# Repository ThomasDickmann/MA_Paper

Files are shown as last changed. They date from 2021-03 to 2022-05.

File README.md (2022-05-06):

# An adaptive mechatronic exoskeleton for force-controlled finger rehabilitation
>This repository represents the source code for a novel mechatronic exoskeleton architecture for finger rehabilitation. The system consists of an underactuated kinematic structure that enables the exoskeleton to act as an adaptive finger stimulator. 

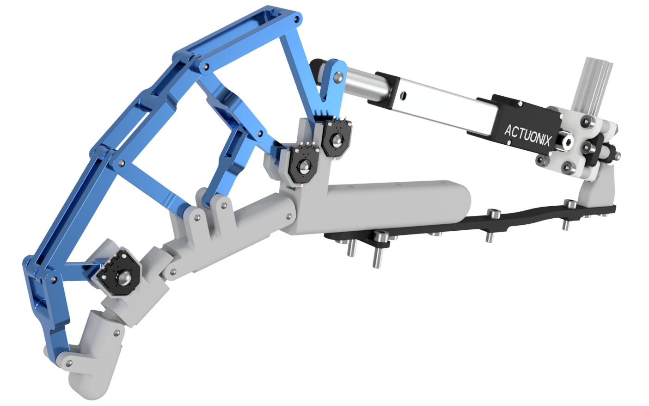
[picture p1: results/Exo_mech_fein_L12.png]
 

## Setup

* Install Matlab

## What does each file do? 

    .     
    ├── MATLAB_Functions                 # Folder for all functions in 'm' format
    |   |
    │   ├── CSV_Interpretation.m         # calculates diagnostic data from .csv
    │   ├── getActuationAngle.m          # determines the angle phi_1 at point B depending the actor
    │   ├── getActuationForce.m          # calculates the external force of the actuator
    │   ├── getActuationSignal.m         # determines the delta_s position of the actuator from phi_1
    │   ├── getAngle.m                   # finds the angle of a vector (r_i) in the worldframe
    │   ├── getConstParam.m              # calculation of the const parameters depending on the finger
    │   ├── getExtForces.m               # determines the external forces of the exoskeleton
    │   ├── getJointAngles.m             # calculates the finger joint angles from the joint positions
    │   ├── getJointAnglesDeg.m          # in Degrees
    │   ├── getJointAnglesRad.m          # in Rad
    │   ├── getJointTorques.m            # calculates the finger moments for the quasistatic state
    │   ├── getKinConfig.m               # position of all joints of the kinematics from the encoders
    │   ├── getPhalanxForces.m           # rotates the external forces on the phalanges
    │   ├── getPoint.m                   # position of a joint in the world system
    │   ├── plotBR.m                     # plots the range of motion of the index finger
    │   ├── plotBR_alternative.m         # alternative to plotBR.m
    │   └── plotKinConfig.m              # plots the current kinematic position 
    |
    ├── MATLAB_Models                    # Folder for all models in 'm' format 
    |   |
    |   ├── Calibration_curves_potentiometer.m        # contains the calibration data of the position sensors
    |   ├── Force_Equilibrium_SoE.m                   # creates a linear system of equations from the equilibrium conditions around each joint
    |   ├── Force_Sensor_Drift_Hysteresis_Test.m      # interpretation of force sensor data
    |   ├── Integrated_Force_Sensor_test.m            # simplified force sensor calibration for recalibrating the integrated sensors
    |   ├── Interpretation_Script_CSV_Files.m         # script which utilizes the CSV_Interpretation.m function to create arrays with interpreted data
    |   ├── Linear_Interpolation_Potentiometer.m      # linear interpolation concept used for position sensor calibration  
    |   ├── Newton_Euler_generation_script.m          # creates the full NE model of the finger using the symbolic toolbox
    |   ├── Plot_ROM_Index_Finger.m                   # plots the range of motion of the index finger based on joint angle data arrays
    |   ├── Plot_interpreted_CSV_values.m             # plots the interpreted .csv test data
    |   ├── Single_sensor_dataset_interpretation.m    # exemplary interpretation of a singe test data set (3 joint angles, 2 forces)
    |   
    └── results.txt                      # Folder for all result images, test data and CAD files for printing (.stl)

# Citation

If you use this project in any of your work, please cite:

```
Dickmann  T, Wilhelm NJ, Glowalla  C, Haddadin  S, van der Smagt  P and Burgkart  R (2021) An Adaptive Mechatronic Exoskeleton for Force-Controlled Finger Rehabilitation. Front. Robot. AI 8:716451. doi: 10.3389/frobt.2021.716451
```

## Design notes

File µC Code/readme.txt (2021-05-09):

Code for Teensy 4.1 with modified Teensyduino Beta Version -> Enables usage of standard <sd.h> library/commands with <sdfat.h> functionality

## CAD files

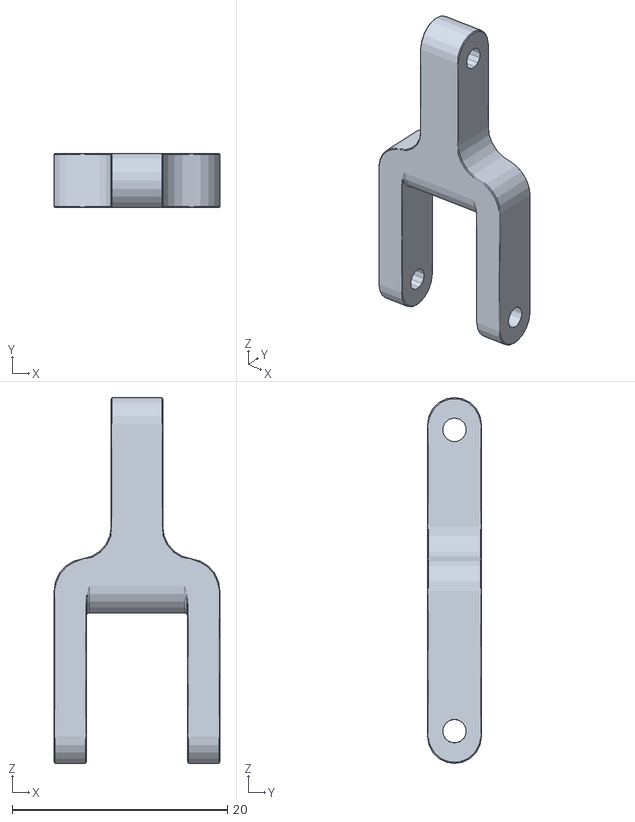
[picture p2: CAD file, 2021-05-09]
results/CAD/l_12.stl
15.4 x 5.00 x 34.0

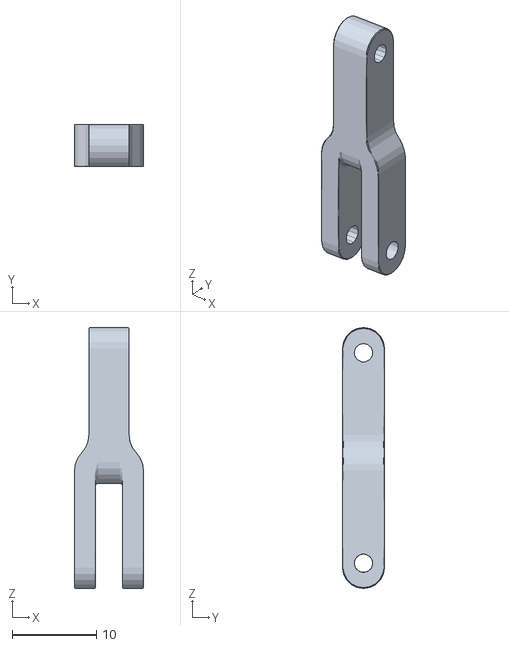
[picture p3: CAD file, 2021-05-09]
results/CAD/l_6.stl
8.20 x 5.00 x 31.0

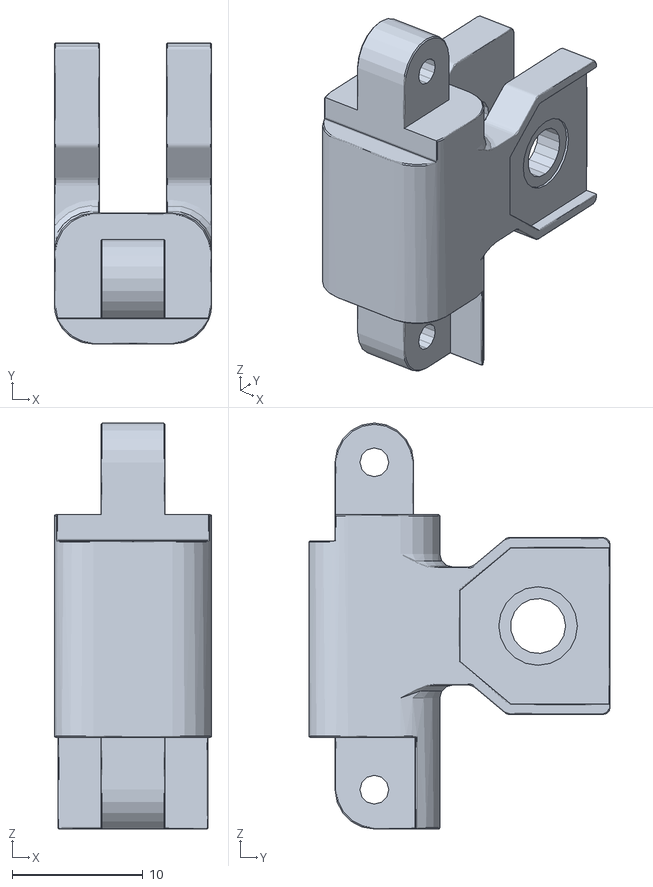
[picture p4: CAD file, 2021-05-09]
results/CAD/Phalanx_Media.stl
12.0 x 23.0 x 31.0

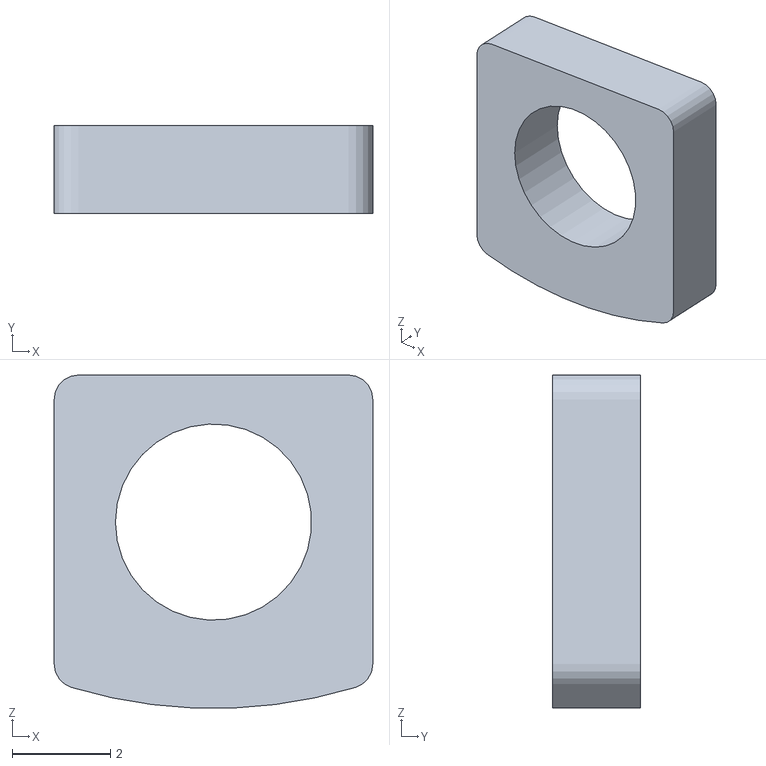
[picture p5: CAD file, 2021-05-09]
results/CAD/Aktor_Inlay.stl
6.50 x 1.80 x 6.79

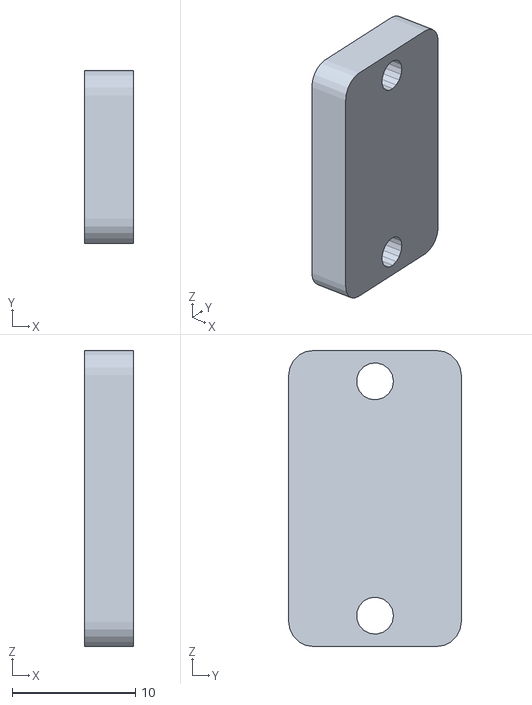
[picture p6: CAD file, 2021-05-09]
results/CAD/Sensoraufnahme.stl
4.00 x 14.0 x 24.0

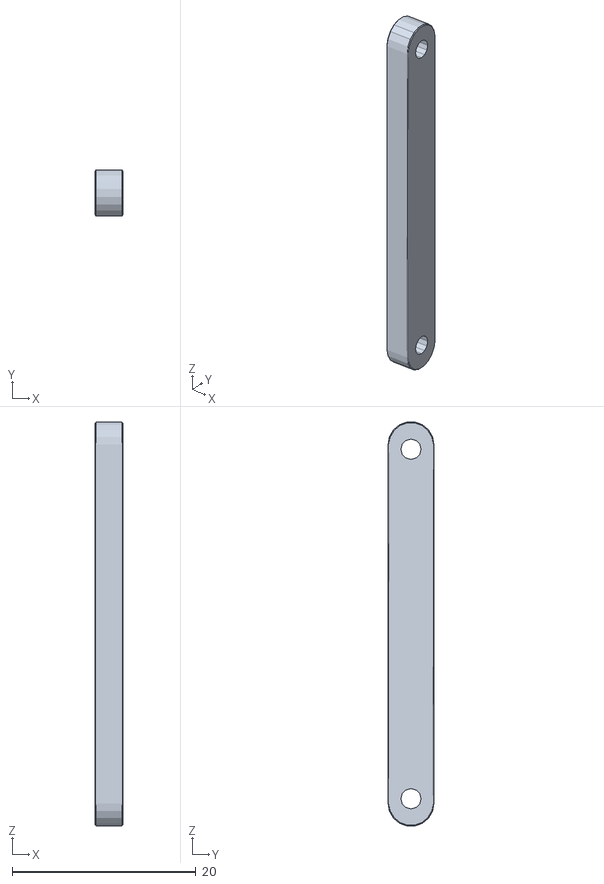
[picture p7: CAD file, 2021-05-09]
results/CAD/l_10__2x_drucken.stl
3.00 x 5.00 x 43.9

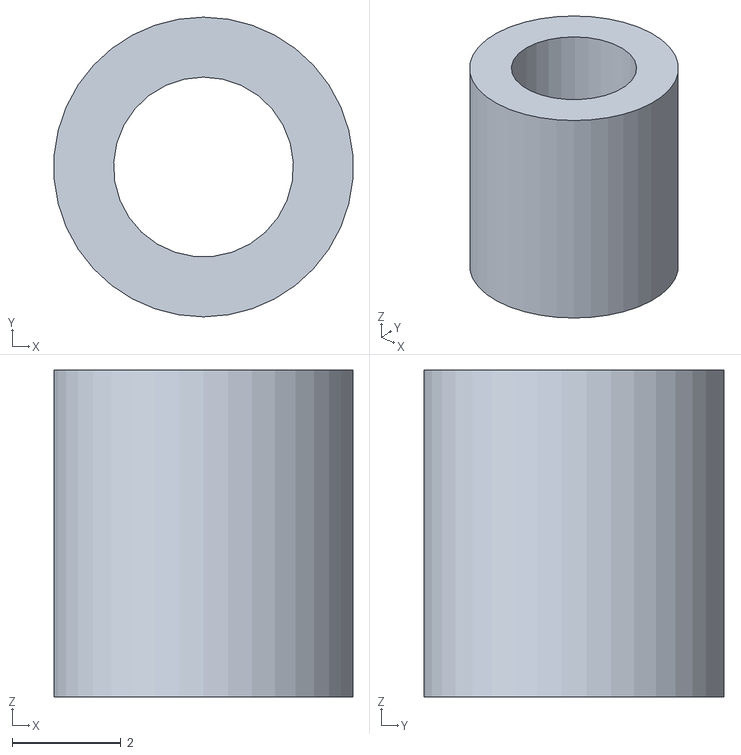
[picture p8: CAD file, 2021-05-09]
results/CAD/Standoffs_6x.stl
5.48 x 5.50 x 6.00

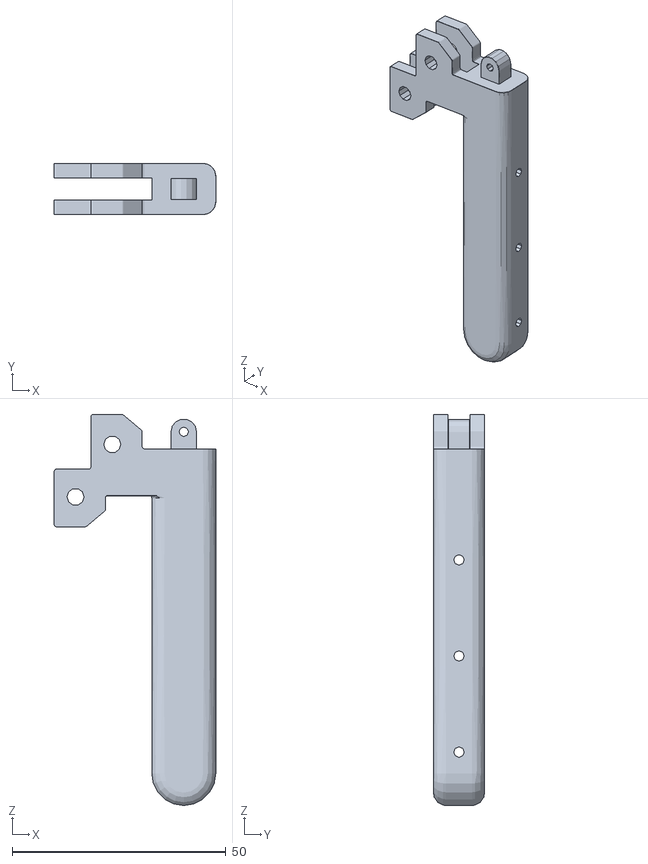
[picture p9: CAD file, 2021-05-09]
results/CAD/Metacarpal.stl
37.8 x 12.0 x 91.5

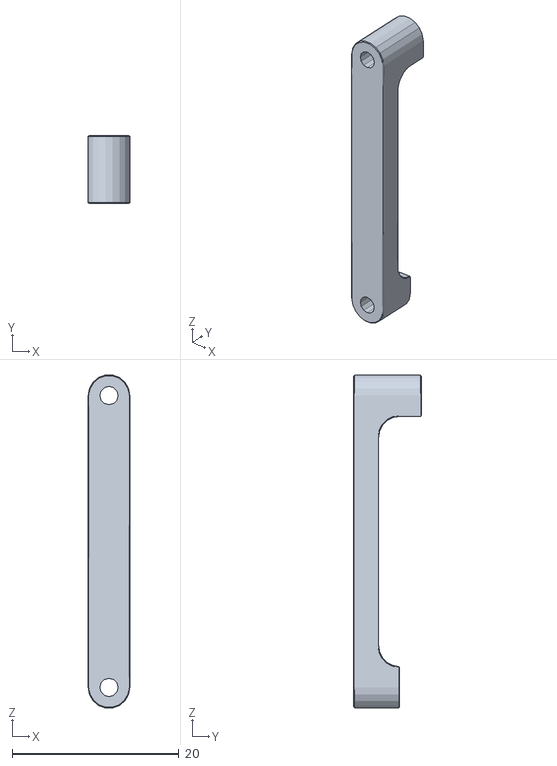
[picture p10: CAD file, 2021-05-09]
results/CAD/l_2__2x_drucken.stl
5.00 x 8.10 x 39.9

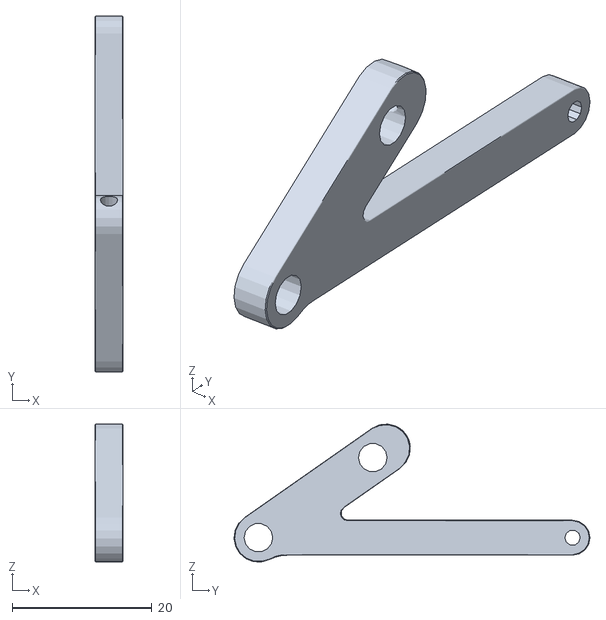
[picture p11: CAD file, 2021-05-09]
results/CAD/l_1.stl
4.00 x 51.0 x 19.7

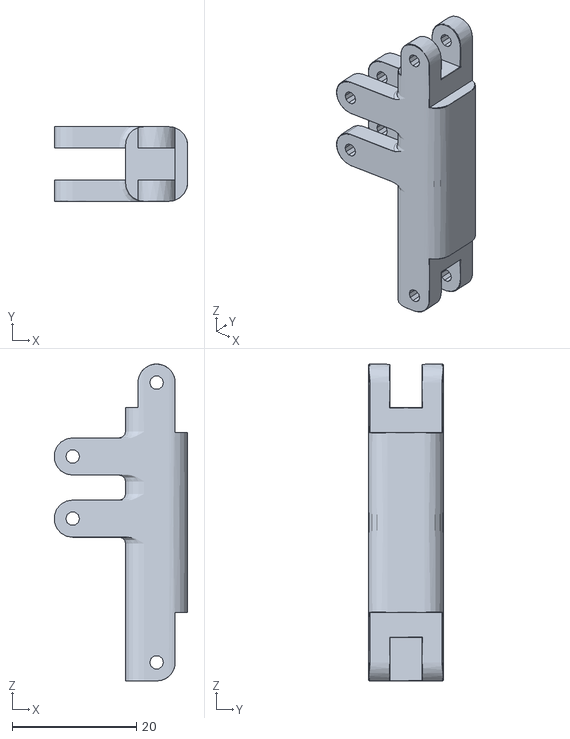
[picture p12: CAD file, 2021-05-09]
results/CAD/Phalanx_Proximalis.stl
21.5 x 12.0 x 51.0

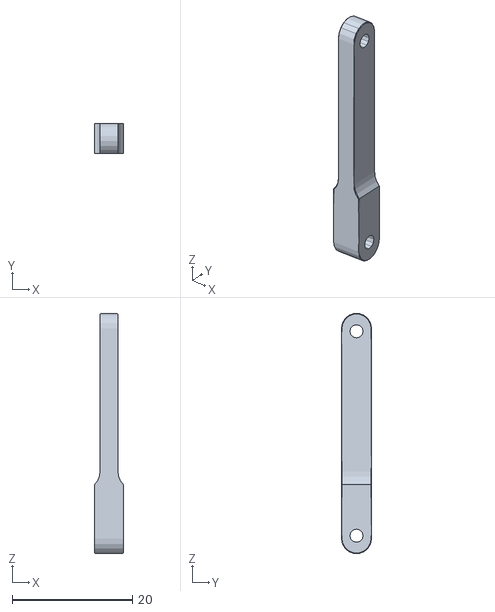
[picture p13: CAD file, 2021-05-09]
results/CAD/l_8.stl
4.80 x 5.00 x 39.9

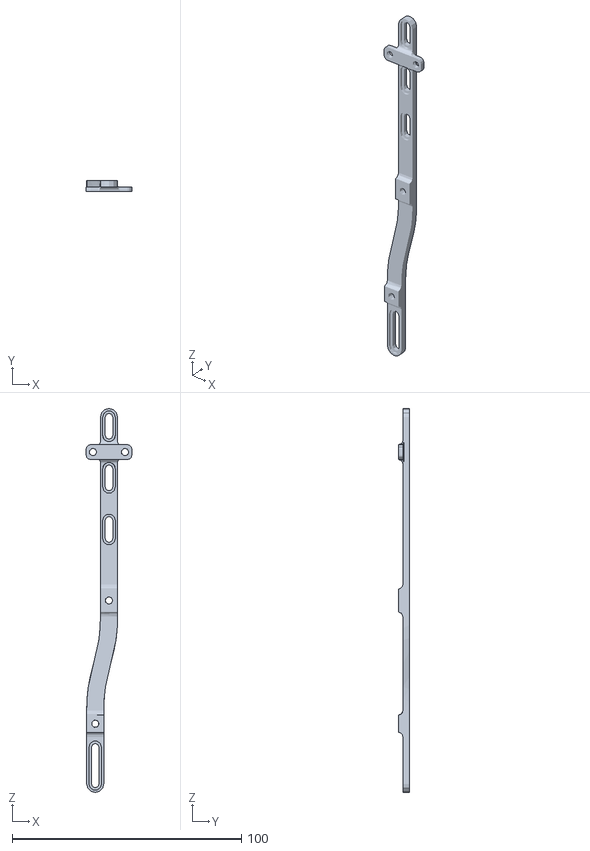
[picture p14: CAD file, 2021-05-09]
results/CAD/Aktoraufnahme.stl
20.0 x 5.00 x 167.5

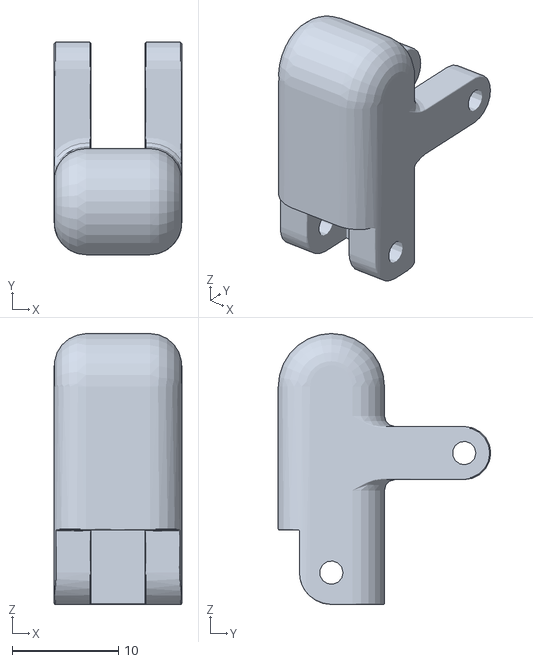
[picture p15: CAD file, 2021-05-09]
results/CAD/Phalanx_Distalis.stl
12.0 x 20.0 x 25.5

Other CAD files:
results/CAD/l_3.stl
results/CAD/l_7.stl
results/CAD/Att_Base.stl
results/CAD/Klemmelement_2x.stl
results/CAD/Gelenkmount.stl
results/CAD/Mount.stl
results/CAD/l_11.stl
results/CAD/l_4.stl

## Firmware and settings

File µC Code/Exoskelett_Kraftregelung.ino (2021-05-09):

#include <SD.h>
#include <math.h> 

//Vorbereitung SD Karte /////////////////////////////////////////////
File dataFile; //Fileobjekt für SD Karte erzeugen

//Aufruf in Setup, Karteninitialisierung
void initCard()
{
  bool ret;
  Serial.print("Initialisiere SD Karte...");
  ret = SD.begin(BUILTIN_SDCARD);
  if (!ret) {
    Serial.println("Card failed, or not present");
    while (1) {
    }
  }
  Serial.println("Karte initialisiert.");
  }

//Aufruf in Setup, Vorbereitung des dataFile zum beschreiben
bool openFile_write(const char *filename)
{
  dataFile = SD.open(filename, FILE_WRITE);  
  dataFile.flush();
  return (dataFile==true);
}
///////////////////////////////////////////////////////////////////////

//Laufzeit und Loggingfrequenz einstellen ////////////////////////////
//Setzen von fester Loopedauer über Timer im Hintergrund, sodass der Controller parallel arbeiten kann
unsigned int loopTime = 10; //Wert für gewünschtes Loopintervall in Millisekunden
unsigned long breakTime; //Zeitstempel zu Anfang des Loops -> Ablegen des Zeitpunkts für Loopende

//Counter für gewünschte Anzahl an Loopdurchläufen 
int totalRuns = 25000/loopTime; //(25 Sekunden pro Bewegung)
int t = 0; //Zählervariable für Loopdurchläufe
int k = 0; //Zählervariable für Funktion Aktortrajektorie
///////////////////////////////////////////////////////////////////////

//Verzögerung für Kraftsensormessungen 

int t_del = 3000;

//Parametrierung der Aktorik///////////////////////////////////////////
const float l_akt = 139.3f; //102mm Aktorlänge von Loch zu Loch + Kraftsensorlänge von 37.3mm 
const float d_b = 161.062f; //Abstand Glelenk B zu Mountgelenk Aktorrückseite
const float akt_x = -160.761f; //Abstand in X-Richtung Welt KS Gelenk B zu Mountgelenk Aktorrückseite in mm 
const float akt_y = -9.845f; //Abstand Y-Richtung Gelenk B zu Mountgelenk Aktorrückseite in mm 
const float alpha_const = 0.0612f; //Winkel zwischen d_B und X-Achse Weltsysten in rad (3.5°)
const float theta = 0.6109f; //Winkel zwischen l_1 und l_2 in rad (35°)
const float l_s = 20.0f; //Kurzer Arm der Antriebsschwinge
//const float phi_B_min = 0.3491f; //20°, Minimalwert des Schwingenwinkels -> Berechnung max. Aktorstellung
const float phi_B_max = 2.2340f; //128°, Maximalwert des Schwingenwinkels -> Berechnung min. Aktorstellung 
//Überschreiben für Demo: Weniger Auslenkung
const float phi_B_min = 0.9235f; //30°
const float delta_phi_max = 108.000f; //Maximales Intervall der Antriebsschwinge in Grad
const float val_count_phi_B_max = 5.0f; //Startwert für Loopcounter, sodass Aktor aus seiner Minimalposition heraus startet (Anfahren in Setup-Funktion!)
const float pi = 3.1416f; //Konstante für Wert von pi erzeugen 
const float multip = (2*pi)/totalRuns; //Aufteilung von 2pi auf die gesamte Anzahl an Durchläufen
///////////////////////////////////////////////////////////////////////


//Funktionen zur Berechnung der Aktorvariablen/////////////////////////
//Berechnungen von Sollstellung s des Aktors aus Schwingenwinkelvorgabe [Verifiziert durch Vergleich mit MATLAB]
float getActuationSignal (float phi){
    float alpha = pi - theta - phi + alpha_const;
    //Serial.print("alpha= ");
    //Serial.println(alpha);
    float l = sqrtf((powf(l_s,2) + powf(d_b,2) - 2*l_s*d_b*cosf(alpha))); //Kosinussatz zur Berechnung der Gesamtlänge des Aktorverbands l
    //Serial.print("l= ");
    //Serial.println(l);
    float s_nom = l - l_akt;
    return s_nom; 
}

//Berechnung des aktuell anliegenden Antriebsmoments aus Schwingenwinkel und gemessener Aktorkraft [Verifiziert durch Vergleich mit MATLAB]
float getActuationTorque (float phi_B, float F_Aktor){
    float alpha_quer = pi - theta - phi_B;  //Winkel zwischen X-Achse und l_s
    //Serial.print("alpha_quer= ");
    //Serial.println(alpha_quer);
    float S_x = -l_s * cosf(alpha_quer); //x-Position der Spitze des kurzen Schwingenarms 
    float S_y = l_s * sinf(alpha_quer); //y-Position der Spitze des kurzen Schwingenarms 
    float phi_F = getAngle(akt_x,akt_y,S_x,S_y); // Funktion: Berechnet aktuellen Kraftvektorwinkel im Raum 
    //Serial.print("phi_F= ");
    //Serial.println(phi_F);
    float F_Akt_x = F_Aktor * cosf(phi_F); //Komponenten des Kraftvektors in Weltsystem
    float F_Akt_y = F_Aktor * sinf(phi_F);
    float M_akt = (F_Akt_x * S_y + F_Akt_y * (-S_x));  //[Nmm], Berechnen des Moments um Punkt B, pos. Richtung s. Skizze, pos. delta_x führt zu neg. Moment nach Skizze  
    return fabs(M_akt);
}

//Benötigte Funktion zur Berechnung des Kraftvektorwinkels [Verifiziert durch Vergleich mit MATLAB]
float getAngle(float p1_x, float p1_y, float p2_x, float p2_y){
    float delta_x = p2_x - p1_x; //akt_x und akt_y konst. Größen definiert in aktorik.h
    float delta_y = p2_y - p1_y;  
    float phi = 0;     
    if (delta_x > 0){
       phi = atanf(delta_y/delta_x);}
    else if (delta_x < 0){
       phi = atanf(delta_y/delta_x) - pi;}
    else if (delta_x == 0 && delta_y > 0){
       phi = pi/2; } 
    else if (delta_x == 0 && delta_y < 0){
       phi = -pi/2; }
    return phi;
}
///////////////////////////////////////////////////////////////////////

// Funktionen zur Aktorsteuerung //////////////////////////////////////

//Signalpin PWM-Output für Aktor (Kopie von oben)
const int aktorpin = 29;
 
//Berechnung der nominellen Position des Aktors, aus nominellem Schwingenwinkel phi_B, aus Timer/Counter t (Zahl Loopdurchläufe) [Verifiziert mit MATLAB]
float getNomPosition (int k){
    //Berechnung des nominellen Schwingenwinkels aus Loopcounter
    float sinsig = k * multip; //Winkelstellung des Sinussignals basierend auf Loopdurchlaufnummer berechnen (Intervall 0-2*pi auf 10s)
    //Serial.print("sinsig= ");
    //Serial.println(sinsig);
    float phi_raw = sinf(sinsig + 0.5*pi); //Sinusschwingung 0.1Hz mit Amplitude [-1,1], Phasenverschiebung um pi/2, sodass bei counter = 0 (Bewegungsbeginn) mit Maximalwert gestartet wird
    //Serial.print("phi_raw= ");
    //Serial.println(phi_raw);
    float phi_d = (phi_raw * delta_phi_max/2); //Skalierungsfakor ist halbes maximales Winkelintervall
    //Serial.print("phi_d ");
    //Serial.println(phi_d);
    phi_d = phi_d + delta_phi_max/2 + (phi_B_min/pi) * 180; // Offsetfaktor positioniert das Intervall richtig in y-Richtung, sodass phi_B_max erreicht wird (Angegeben in Grad)
    //Serial.print("phi_d ");
    //Serial.println(phi_d);
    float phi_r = (phi_d / 180) * pi; //Konvertierung des nominellen Schwingenwinkels von Deg nach Rad
    //Serial.print("phi_r ");
    //Serial.println(phi_r);
    //Berechnung der korrespondierenden Schubstangenposition
    float nomPosition = getActuationSignal (phi_r); 
    return nomPosition;
} 

//Funktion zum Mappen von Kommazahlen [Tested]
float mapf(float x, float in_min, float in_max, float out_min, float out_max){ 
    float val_mapped = (x - in_min) * (out_max - out_min) / (in_max - in_min) + out_min;
    return val_mapped;
}

//Mappen des Ausgangssignals auf max. Range des Aktors (0-3.3V PWM = 0-33mm Aktorzustellung) [Tested]
float mapActuatorInput(float nomPosition){
  //Max. Range Aktor 0-33mm, max. Range Input = 0-34.01mm
  float nomPositionMapped = mapf(nomPosition, 0, 34.01, 0, 33);
  return nomPositionMapped;
}


//Ansteuern des Aktors basierend auf in Loop vorgegebenem Sollwert für s
void positionActuator(int k){
  //Bestimmen der nominellen Aktorposition basieren auf Loopdurchlauf
  float nomPos = getNomPosition(k);
  //Mappen der nominellen Position auf Range des Aktors 
   float nomPosMapped = mapActuatorInput(nomPos);
  //Schreiben der Position als PWM Signal am Aktorpin //Begrenzte Auflösung AnalogWrite!
  int nomPosInt = nomPosMapped*1000;
  int outputsignal = map(nomPosInt, 0, 33000, 0, 256); //Range analogWrite von 0-256, Umrechnen der Kommawerte in der Position auf int Werte 
  //Serial.print("Outputsignal ");
  //Serial.println(outputsignal); 
  analogWrite(aktorpin, outputsignal); 
}

///////////////////////////////////////////////////////////////////////


//Funktionen zur Verarbeitung des eingelesenen Positionssensors an Gelenk B/////////////
//Positionssensoren: 
unsigned int readAngleRadB (int potipin){
  unsigned int rawData = analogRead(potipin); 
  unsigned int DataMapped = rawData; //TODO: Verarbeitung der Kalibrierungskurven
  //Geradengleichung benutzen, um kalibrierte Winkelstellung aus ADC Wert zu berechnen
  return DataMapped;  
}

//Wegen verschiedenen Kalibriergrade werden eigene Funktionen für jeden Sensor gebraucht! 
///////////////////////////////////////////////////////////////////////


//Funktionen zur Verstellung der Aktors////////////////////////////////
//Bestimmen des Stellsignals
//float getNomPosition (float nomPhi) {
//  return PosNom; 
//}

//Manuelle Verstellung des Aktors über Drehpoti
void posManual (int inputpin, int aktorpin){
  int intputsignal = analogRead(inputpin);
  int outputsignal = map(intputsignal, 0, 1023, 0, 333); 
  Serial.println(outputsignal); 
  analogWrite(aktorpin, outputsignal); 
}

//////////////////////////////////////////////////////////////////////


//Zuweisen der MCU Pins ///////////////////////////////////////////////
const int inputpin = A10; 

//Positionssensorik
const int potiA = A13; 
const int potiB = A12; 
const int potiK = A11;

//Kraftsensorik 
const int fSenB = A17; //Pin41
const int fSenA = A16; //Pin40

//Signalpin PWM-Output für Aktor (Kopie von oben)
//const int aktorpin = 29; 
////////////////////////////////////////////////////////////////////////

unsigned long setupTime;

//Kraftregelung
int sensorpin = A17;
int dir = 1; //Flag für Richtung R=1 vorwärts, R=0 rückwärts
int per = 1; //Flag für aktuelle Periode 1:(0,pi) oder Periode 2:(pi,2pi)
int valSens; //Analog eingelesenen Sensorwert, soll Kraftwert simulieren 

float M_upper = 0.07 ; //Oberer Grenzwert für Moment [Nm] -> Umkehrung von Vorwärts nach Rückwärts
float M_lower = 0.01; //Unterer Grenzwert für Moment -> Umkehrung von Rückwärts nach Vorwärts


void setup() {
  
  analogWriteFrequency(aktorpin, 1000); // PWM Frequenz des Aktorpins auf 1 kHz festlegen

   //Anfahren der Ausgangsposition des Aktors (Maximale Extension des Finger)  
  positionActuator(0);
  
  Serial.begin(9600); //Starten Serial Monitor
  while(!Serial); //Warten, bis Serial Monitor geöffnet
  delay(2000); 
  
  pinMode(aktorpin, OUTPUT); 

  //Einstellungen für den ADC: Auflösung und Glättung der Messwerte
  analogReadResolution(12);
  analogReadAveraging(32); //8, 16, 32

  //Vorbereiten der SD Karte für Schreiben (Funktionen von Frank) 
  initCard();
  openFile_write("log_1.txt");

  //Anfahren der Ausgangsposition des Aktors (Maximale Extension des Finger)  
  positionActuator(0);

  setupTime = millis();
}




  
  void loop() {

  //Positionieren des Aktors nach Loopdurchlaufsnummer 
  positionActuator(k);
  
  //Zeitstempel: Aktueller Loopdurchlauf (Startet bei 0)
  unsigned long ms = millis() - setupTime; 

   //Wert für Endzeitpunkt von aktuellem Loop erzeugen
  breakTime = millis() + loopTime; 
  //Serial.print("Loop startet: ");

  //Einlesen der Positionssensorik (Potentiometer)
  unsigned int angleA = analogRead(potiA);
  unsigned int angleB = analogRead(potiB);
  //Ueberschreiben mit fixem ADC Wert für Demo 
  //angleB = 2600;
  unsigned int angleK = analogRead(potiK);
  
  /*
  //Mappen der Sensordaten auf Winkelwerte:
  //TODO
  Serial.print("Winkel B: ");
  Serial.print(angleB); 
  Serial.print("   Winkel A: ");
  Serial.print(angleA); 
  Serial.print("   Winkel K: ");
  Serial.println(angleK);
  */

  //Einlesen der Kraftsensorik (A201s)
  unsigned int forceB = analogRead(fSenB); //Sensor oben, Anschluss an GND Seite
  unsigned int forceA = analogRead(fSenA);  //Sensor unten, Anschluss an VCC Seite

  //Mappen der Sensordaten auf Winkelwerte:
  //TODO
  Serial.print("   Kraft Sensor B (vorne, Druck): ");
  Serial.print(forceB); 
  Serial.print("   Kraft Sensor A (hinten, Zug): ");
  Serial.println(forceA); 
  
  
  //Serial.print("Loop Nummer ");
  //Serial.println(t);
  
  //Bestimmen des momentanen Schwingenwinkels
  float   phi_B_d = 0.0788*angleB - 114.2788; //Umrechnung des ADC Werts über lineare Regression von für Positionssensorik an Gelenk B
  float   phi_B = phi_B_d*(pi/180); //Umrechnung des Winkels in Radiant 
  //Serial.print("Winkel B berechnet = ");
  //Serial.println(phi_B_d);
 /* float   phi_A_d = 0.0843*angleA - 206.2727; //Umrechnung des ADC Werts über lineare Regression von für Positionssensorik an Gelenk A
  float   phi_A = phi_A_d*(pi/180); //Umrechnung des Winkels in Radiant 
  //Serial.print("Winkel A berechnet = ");
  //Serial.println(phi_A_d);
  float   phi_K_d = 0.0721*angleK - 88.8166; //Umrechnung des ADC Werts über lineare Regression von für Positionssensorik an Gelenk K
  float   phi_K = phi_K_d*(pi/180); //Umrechnung des Winkels in Radiant 
  //Serial.print("Winkel K berechnet = ");
  //Serial.println(phi_K_d);
*/
  //Bestimmen der Kräfte
  float F_back = 0.0036 *forceA - 2.0806;  //Kraftsensor A 
  float F_front =0.0033 * forceB - 2.2402; //Kraftsensor B
  
  //Berechnen des Antriebsmoments aus Aktorkraft
  float F_akt = F_front - F_back; //Differenz der Kraftsensoren ist aktuelle Aktorkraft auf Kinematik
  float M_akt = getActuationTorque(phi_B,F_akt)/1000; //Nm aus Nmm 
  //Ueberschreiben mit fixem Wert fuer Demo an Hand (keine Positionssensorik verbaut)

  
  //float M_akt = 10; //Regler umgehen, immer Vorwärts
  Serial.print("M_akt = ");
  Serial.println(M_akt);
  
  
  //DEMO KRAFTREGELUNG: Dummywert nutzen (Encoder)
  //M_akt = analogRead(sensorpin); //Kraftwert einlesen 
  //Serial.print("Sensorwert F= ");
  //Serial.println(valSens);

  //Zweipunktregler für Kraftregelung
  //Flagprüfung: Betriebsmodus feststellen 
  switch (dir) {
  case 1: //Richtung = Vorwärts, Oberer Grenzwert relevant
    //Prüfung Kraftgrenzwert
    if (M_akt < M_upper){
      //Grenzwert nicht erreicht, im Modus Vorwärts bleiben
      //Begrenzung auf maximalen Wert totalRuns
     k++; //Variable für Schwingenwinkel um 1 erhöhen
     }
     else {
      //Grenzwert überschritten, umkehren der Bewegungsrichtung in Rückwärts
      dir=0; //Umschalten der Flagvariable für Richtung
      Serial.println("oberer Grenzwert überschritten, Wechsel in Rückwärtsbewegung");
    }
    break;
  case 0: //Richtung = Rückwärts, unterer Grenzwert relevant
    //Prüfung Kraftgrenzwert
    if (M_akt > M_lower){
      //Grenzwert immer noch zu hoch, im Modus rückwärts bleiben 

      //WICHTIG: Periodizität beachten!
      //In erster Periode darf nach einer Bewegungsumkehrung nicht unter 0 gefahren werden
      //In zweiter Periode darf nach Bewegungsumkehrung nicht unter pi gefahren werden 
      //Andernfalls wird der kritische Winkel nach Umkehr der Bewegung wegen Periodizität erzeut durchschritten!

        switch(per){
        case 1: //Periode 1
           if (k > 0){
              k--; 
           }
           else { 
                //nicht weiter reduzieren (Periodizität)
           }
        break; 
        case 2: //Periode 2
            if (k > totalRuns/2){
                 k--; 
            }
            else { 
            //nicht weiter reduzieren (Periodizität)
            }
        break;
        }//Ende der Fallunterscheidung Periode
    }//Ende Fall Grenzwert zu hoch
    
    else {
      //Kraftwert ausreichen abgefallen, umkehren der Bewegungsrichtung in Vorwärts
      dir=1; //Umschalten der Flagvariable für Richtung
      Serial.println("unterer Grenzwert unterschritten, wechsel in Vorwärtsbewegung");
    }
    break; //Ende Case Rückwärts
  }//Ende Zweipunktregelung

  //Serial.print("k= ");
  //Serial.println(k);

  if (k<totalRuns/2){
    //Serial.print("Periode = ");
    per = 1;
    //Serial.println(per);
  }
  if (k>totalRuns/2){
    //Serial.print("Periode = 2");
    per = 2;
    //Serial.println(per);
  }
  
  //Schreiben der erhobenen Daten auf die SD Karte als 32Byte String
  dataFile.printf("%5u;%4u;%4u;%4u;%4u;%4u\r\n", ms, angleB, angleA, angleK, forceA, forceB);
  
   //Prüfen der Abbruchbedingung: Beenden der Messungen nach Anzahl totalRuns Loopdurchläufen
  if (t++ > totalRuns) {
    dataFile.close();
    Serial.println("Messungen abgeschlossen, Programm beendet");
    while(1);
  } //Durchgang

  //Prüfen, ob gesetzte Soll-Loopzeit verstrichen ist - wenn nicht, warten bis neuer Loop beginnen kann 
  while(millis() < breakTime){
      //waiting for loop time to finish - do nothing
   } //Loopdauer
  
} //Loop Funktion
